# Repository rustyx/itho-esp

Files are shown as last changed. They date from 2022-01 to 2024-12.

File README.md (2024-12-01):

## itho-esp

Itho diag port controller

### WTF is this?

This is an ESP32 firmware that connects to the dianostic port of an Itho device in order to communicate with it and let it do things it couldn't before.

Originally designed for controlling the Itho HRU ecofan 350 ventilation unit via MQTT, but can be used to play with the I2C bus of many other Itho products.

Some key features are:

* I2C bus sniffing - dumps messages to/from the Itho CPU. On products that have peripherals like an RFT receiver, will dump traffic between the peripheral and the CPU.
* Send and receive dianostic messages to the CPU.
* Query the device status and parse parameter values.
* Control the device via Wi-Fi/MQTT.
* Monitor temperature and humidity via DHT22 and/or SHT4x, publish results via MQTT.
* (HRU-specific) Control ventilation level setting (low, med., high) via MQTT.
* (HRU-specific) Automatically set ventilation to high when humidity exceeds a threshold value.

### Prerequisites

Hardware:

* An Itho ecofan HRU 350 WTW unit (or another Itho product that has an RJ45 diagnostic port)
* ESP32 Dev Kit (or a raw ESP32 unit + power supply + a USB COM dongle + some SMD work)
* a logic level shifter for converting 5V <-> 3,3V logic levels (or 2 small N-channel MOSFETs)
* One or more DHT22 or SHT4x (optional, to measure humidity)
* DC-DC buck converter (optional, to power ESP32 directly from the Itho diag port's +15V)

Software:

* [ESP-IDF Framework](https://docs.espressif.com/projects/esp-idf/en/latest/esp32/get-started/index.html) v5.3+ and its prerequisites (`xtensa-esp32-elf-gcc`, `pip`, etc.)
* USB COM driver matching the USB serial interface chip (see [Connect ESP32 to PC](https://docs.espressif.com/projects/esp-idf/en/latest/esp32/get-started/establish-serial-connection.html))
* [Visual Studio Code](https://code.visualstudio.com/download) with [ESP-IDF extension](https://github.com/espressif/vscode-esp-idf-extension/blob/master/docs/ONBOARDING.md) (optional but recommended, will also help with installing the ESP-IDF framework)

### Building

* Make sure the ESP Dev Kit can be connected to USB and a COM port is functional
* Install ESP-IDF framework, make sure it works and has access to the COM port (see [connect your device](https://docs.espressif.com/projects/esp-idf/en/latest/esp32/get-started/#get-started-connect))
* Build the firmware: `idf.py build`
* Flash the firmware: `idf.py -b 921600 flash` (will also invoke `build` if needed)  
  To flash, the ESP32 chip needs to be put in download mode. This can be achieved by shorting J3 pin 5 to ground (pin 4) while booting.
* Attach to the console: `idf.py monitor` (can combine with the `flash` command)

### Console interface

* `config` : Configure Wi-Fi, MQTT and humidity sensor GPIO
* `p` : Pullup OFF
* `P` : Pullup ON
* `s` : Sniffer OFF
* `S` : Sniffer ON
* `h` : Hex reporting OFF
* `H` : Hex reporting ON
* Or any of MQTT command below

### MQTT commands

* `set1` - set ventilation level to low
* `set2` - set ventilation level to medium
* `set3` - set ventilation level to high for 30 min (then back to low)
* `hum` - request DHT22 temp/humidity values
* `status` - request device status
* `ping` - request `pong`
* `high_hum_threshold` - get current high humidity threshold (output goes to `esp-data-dht`)
* `high_hum_threshold N` - set high humidity threshold to N * 0.1% (e.g. for 75% use 750)
* Hex bytes - send these bytes to the bus

### MQTT topics

`esp` - The topic for MQTT requests.

`esp-data` - The topic for MQTT replies. In addition, Itho status data + DHT data are published here as a JSON array every 5 seconds.

`esp-data-dht` - DHT data (humidity, temp, status) is published here when `hum` is requested.

`esp-data-hex` - when hex reporting is enabled, all Itho response messages are published here in hex format.

### Tech specs

For technical details and other research notes refer to [Specs.md](Specs.md)

### License

The unlicense:

The software is provided AS-IS without any warranty.

You can do whatever you want with it to the extent permitted by law.

I will deny any involvement with this project, should any questions arise.

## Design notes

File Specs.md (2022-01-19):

### RJ45 dianostic port pinout

| Pin | |
| --- | ---- |
| 2 | SCL  |
| 3 | GND  |
| 4 | GND  |
| 5 | +15V |
| 7 | SDA  |

The SCL, SDA are I2C lines with a 5V pull-up (5,6K) connecting straight to the CPU on the Itho mainboard.

+15V can be used for power supply needs (appears to be good for at least 1A).

There is no +5V available, but is not needed due to the built-in pull-ups (the lines only need to be pulled down for a logical 0).

---

### GPIO Pin assignment

| GPIO | Desc | Notes |
| ---- | --- | --- |
| 0 | Reset | The ESP32 reset pin (inverted) |
| 13 | I2C Sniffer SDA | Defined in [i2c_sniffer.h](main/i2c_sniffer.h) |
| 14 | I2C Slave SDA | Defined in [i2c_slave.h](main/i2c_slave.h) |
| 15 | DHT22 I/O | Defined in [dht.h](main/dht.h) |
| 25 | I2C Sniffer SCL | |
| 26 | I2C Master SCL  | Defined in [i2c_master.h](main/i2c_master.h) |
| 27 | I2C Master SDA  | |
| 33 | I2C Slave SCL | |

The I2C pins were carefully chosen so that they can be wired into a "bus", as can be seen on the schematic:

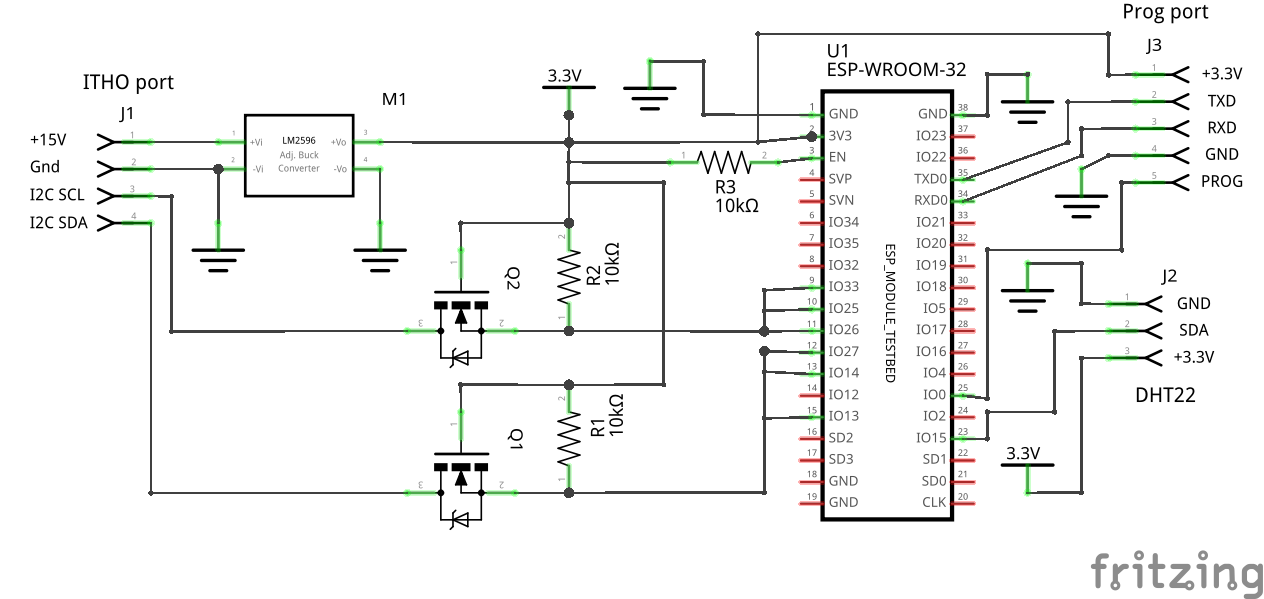
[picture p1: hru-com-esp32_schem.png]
schematic


---

### I2C message format

The Itho mainboard is an I2C master running at ~100kHz.  
Each packet has a checksum byte at the end, which is the negative sum of all other bytes.  
First byte is destination address (0x82 = Itho mainboard).  
Second byte is reply address (0x80 = dongle).  
2 bytes: message code.  
1 byte: message flags (it seems:  `06` = write, `04` = request, `01` = reply).  
1 byte: payload length (N).  
N bytes: payload.  
1 byte: checksum.  

---

### Message `90 E0`: query device type

82 80 90 E0 04 00 8A

Example reply:

80 82 90 E0 01 12 00 01 00 03 12 0B 00 00 00 FF FF FF FF FF FF FF FF 00 62

`00` = Manufacturer (Itho), `03` = Device type (HRU), `12` = HW version, `0B` = list version.

The "list version" refers to the Datalabel_V.. table in the corresponding Jet DB (.par) file of the Servicetool.

Some known Device Type codes:

`01` : Lucht gordijn  
`03` : HRU ECO-fan  
`08` : Laadboiler  
`0A` : Gas gestookte boost boiler  
`0B` : DemandFlow  
`0C` : CO2 relay  
`0D` : Warmtepomp  
`0E` : Oplaadboiler enkele wisselaar  
`0F` : AutoTemp  
`10` : Oplaadboiler dubbele wisselaar  
`11` : RF+  
`14` : CVE  
`15` : Extended  
`16` : Extended Plus  
`1A` : AreaFlow  
`1B` : CVE-Silent  
`1C` : CVE-SilentExt  
`1D` : CVE-SilentExtPlus  
`20` : RF_CO2  
`2B` : HRU 350

---

### Message `90 E1`: query device serial number

82 80 90 E1 04 00 89

Example reply (edited):

80 82 90 E1 01 03 52 D3 3C 48

Serial nr: 52D33C = 5428028

---

### Message `A4 00`: query status format

82 80 A4 00 04 00 56

Example reply:

80 82 A4 00 01 16 91 11 10 90 10 90 92 92 00 92 92 00 00 91 00 10 10 00 90 00 00 10 C8

A4 00 01 followed by number of data elements, followed by element formats (1 byte per element).

Data format (1 byte):

| Bit  | Description |
| ---- | --- |
| 7 | signed (1) / unsigned (0) |
| 6..4 | size in bytes (2^n): 0=1, 1=2, 2=4 |
| 3..0 | decimal digits (divider 10^n) |

So for example `91` would mean "signed, 2 bytes, 0.1 values".

Special cases:

0C: unsigned 1 byte  
0F: unsigned 1 byte * 0.5  
5B: unsigned 2 bytes  
6C: 1 byte boolean

---

### Message `A4 01`: query device status

82 80 A4 01 04 00 55

Example reply:

80 82 A4 01 01 25 00 00 03 9C 03 9E 03 98 03 EB 03 EB 09 09 09 8A 00 09 09 09 8A 00 00 0B B8 01 00 00 00 B1 79 00 00 00 00 10 95 9F

80 82 A4 01 01 followed by data size and data formatted according to the status format (see previous message).

The temperatures are the bytes 09 09 09 8A, or (0x0909 and 0x098A) 23.13 C en 24.42 C respectively (.01 values).

The first 00 00 is the ventilation level. It goes from 0 for position "1" to 03E8 (100.0) for level "3".

For the meaning of each data element refer to [Itho Data Labels.xlsx](Itho%20Data%20Labels.xlsx)

---

### Itho ecofan RFT 536-0124 (RF remote control) messages

Button 1:  
82 60 C1 01 01 11 (4b: msg timestamp) (1b: msg format) (3b: commander ID) (1b: command seq nr) 22 F1 03 00 02 04 (2b: seq) (1b: checksum)

Button 2:  
82 60 C1 01 01 11 (4b: msg timestamp) (1b: msg format) (3b: commander ID) (1b: command seq nr) 22 F1 03 00 03 04 (2b: seq) (1b: checksum)

Button 3:  
82 60 C1 01 01 11 (4b: msg timestamp) (1b: msg format) (3b: commander ID) (1b: command seq nr) 22 F1 03 00 04 04 (2b: seq) (1b: checksum)

Button 4 (1st press):  
82 60 C1 01 01 11 (4b: msg timestamp) (1b: msg format) (3b: commander ID) (1b: command seq nr) 22 F3 03 00 00 0A (2b: seq) (1b: checksum)

Button 4 (2nd press):  
82 60 C1 01 01 11 (4b: msg timestamp) (1b: msg format) (3b: commander ID) (1b: command seq nr) 22 F3 03 00 00 14 (2b: seq) (1b: checksum)

Button 4 (3rd press):  
82 60 C1 01 01 11 (4b: msg timestamp) (1b: msg format) (3b: commander ID) (1b: command seq nr) 22 F3 03 00 00 1E (2b: seq) (1b: checksum)

Register an RFT (press 1+4 or 2+3):  
82 60 C1 01 01 1A (4b: msg timestamp) (1b: msg format) (3b: commander ID) (1b: command seq nr) 1F C9 0C 00 22 F1 (3b: commander ID) 01 10 E0 (3b: commander
ID) (2b: seq) (1b: checksum)

Deregister an RFT (press 1+2+3+4):  
82 60 C1 01 01 14 (4b: msg timestamp) (1b: msg format) (3b: commander ID) (1b: command seq nr) 1F C9 06 00 1F C9 (3b: commander ID) (2b: seq) (1b: checksum)

Notes:

* Each command is repeated 3 times with a short interval
* Note sure if my interpretation of (4b: msg timestamp), (1b: command seq nr), (2b: seq) is correct, most can be `00`'s but some itho devices (but not the HRU) need to have the command seq nr changed every message.
* (3b: commander ID) are the 3 bytes of the device ID
* (1b: msg format) is the message format determining the fields present in the message. For standard 4 button remotes this is `16`.

...

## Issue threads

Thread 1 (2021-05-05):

Datamessage explained a little further

Ierlandfan, 2021-05-05:
Can you explain the data messages a little further? Trying to understand their meanings.

Data format return of an Itho Eco Fan CVS silent: (1B)

80 82 A4 00 01
0C
80 10 10 10 00 10 20 10 10 00 92 92 29
12 datatypes. (0C)  with their formats.
29 is checksum. So far so good.

But then it gets a little blurry.
Status query return:

80 82 A4 01 01

17 64 01 C2 01 C6 00 10 04 02 01 00 00 28 22 00 00 82 00 EF 82 00 82 00 7D

Am I correct that there are 12 size definitions and 12 payloads according to data format and observations?
7d is checksum.

17 64....
64 is payload.
Translates to 100 in decimals.
That would read 10. Is that correct?
10000000 is format, signed, 1 byte, 10^0.

How do the data labels correlate with these?

rustyx, 2021-05-06:
80: signed, 1 byte, 0 decimals
10: unsigned, 2 bytes, 0 decimals
00: unsigned, 1 byte, 0 decimals
20: unsigned, 4 bytes, 0 decimals
92: signed, 2 bytes, 2 decimals (value * 0.01)

So "80 10 10 10 00 10 20 10 10 00 92 92" would be 12 values, for a total of 23 bytes.

Then we group the data bytes according to this definition:

"64 01C2 01C6 0010 04 0201 00002822 0000 8200 EF 8200 8200"

In decimal it becomes

100, 450, 454, 4, 513, 10274, 0, 33280, 239, -322.56, -322.56

Not sure about the formatting of the last two values, it looks strange. What's the full device type response (80 82 90 E0 01...)?

Ierlandfan, 2021-05-06:
Device type:
80 82 90 E0 01 25 00 01 00 1B 37 1B 01 FE FF FF FF FF FF 1D 08 07 E3 43 56 45 2D 52 46 00 00 00 00 00 00 00 00 00 00 00 00 00 00 4E

rustyx, 2021-05-07:
Yes it's a CVE-Silent rev 55, datalabels v.27. Added it to the [Itho Data Labels.xlsx](https://github.com/rustyx/itho-esp/blob/main/Itho%20Data%20Labels.xlsx)

There are 12 data labels which correspond to the values

100, 450, 454, 16, 4, 513, 10274, 0, 33280, 239, -322.56, -322.56

The formatting seems to be correct, so not sure why the weird temp values... do they ever change? If not, then maybe it doesn't have a temp sensor.

Ierlandfan, 2021-05-07:
Now I also understand the datalabels:

Device Type:
80
82 Manufacturergroup
90 Manufacturer
E0
01
25
00
01
00
1B Device (13) CVS_Silent
37 Productversion (55)
1B Listversion (27)

Device (13) correlates (somehow) to the (weak password protected) $_parameters_SilentBasic.par database in the  Itho Service tool. Listversion 27 correlates to Datalabel_V27 in that database.

The temp sensor is indeed not present.

rustyx, 2021-06-15:
Correct, except Device CVS_Silent is 27 (0x1B). Those mappings are hardcoded in the servicetool.

Closed 2021-06-15.

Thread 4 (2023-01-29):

Build fails on undeclared constant ESP_MAC_WIFI_STA

philipkocanda, 2023-01-29:
```
$ idf.py build
```

```
../main/Config.cpp: In member function 'bool Config::Read()':
../main/Config.cpp:39:32: error: 'ESP_MAC_WIFI_STA' was not declared in this scope; did you mean 'ESP_IF_WIFI_STA'?
   39 |     int rc = esp_read_mac(mac, ESP_MAC_WIFI_STA);
      |                                ^~~~~~~~~~~~~~~~
      |                                ESP_IF_WIFI_STA
../main/Config.cpp:39:14: error: 'esp_read_mac' was not declared in this scope
   39 |     int rc = esp_read_mac(mac, ESP_MAC_WIFI_STA);
      |              ^~~~~~~~~~~~
../main/Config.cpp:47:17: error: 'struct mqtt_config_t' has no member named 'client_id'
   47 |     mqtt_config.client_id = mqttId.c_str();
      |                 ^~~~~~~~~
../main/Config.cpp:48:17: error: 'struct mqtt_config_t' has no member named 'uri'
   48 |     mqtt_config.uri = mqtturi.c_str();
      |                 ^~~
../main/Config.cpp:49:17: error: 'struct mqtt_config_t' has no member named 'cert_pem'
   49 |     mqtt_config.cert_pem = trimToNull(mqttServerCert.c_str());
      |                 ^~~~~~~~
../main/Config.cpp:50:17: error: 'struct mqtt_config_t' has no member named 'client_key_pem'
   50 |     mqtt_config.client_key_pem = trimToNull(mqttClientKey.c_str());
      |                 ^~~~~~~~~~~~~~
../main/Config.cpp:51:17: error: 'struct mqtt_config_t' has no member named 'client_cert_pem'
   51 |     mqtt_config.client_cert_pem = trimToNull(mqttClientCert.c_str());
      |                 ^~~~~~~~~~~~~~~
```

Environment:
- Ubuntu 20.04 (amd64)
- ESP-IDF v5.1-dev-3066-g236fa5e669

philipkocanda, 2023-01-29:
Never mind, downgraded to ESP-IDF v4.4 and it compiled without issues. In case anyone is looking for it, here's how to do it (will remove existing esp-idf version):

```sh
cd ~/esp
rm -rf esp-idf
git clone -b v4.4.3 --recursive https://github.com/espressif/esp-idf.git

cd ~/esp/esp-idf
./install.sh esp32
```

Closed 2023-01-29.

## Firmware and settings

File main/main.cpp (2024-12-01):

#include "Config.h"
#include "Nvs.h"
#include "console.h"
#include "dht.h"
#include "sht4x.h"
#include "i2c_master.h"
#include "i2c_slave.h"
#include "i2c_sniffer.h"
#include "mqtt.h"
#include "util.h"
#include "wifi.h"
#include <algorithm>
#include <driver/uart.h>
#include <esp_event.h>
#include <esp_log.h>
#include <esp_system.h>
#include <freertos/FreeRTOS.h>
#include <freertos/event_groups.h>
#include <freertos/queue.h>
#include <freertos/task.h>
#include <string.h>

static const char* TAG = "main";

static char cmd[128];
static uint8_t buf[128];
static uint32_t cmdlen = 0;
static struct {
    int ret = -1, hum = -1, temp = -1;
} dht_ret[max_sensors];
static bool verbose = false, reportHex = false;

Nvs nvs;
Config config;

bool sendBytes(const uint8_t* buf, size_t len) {
    if (len) {
        esp_err_t rc = i2c_master_send((char*)buf, len);
        if (rc || verbose) {
            printf("Master send: %d\n", rc);
        }
        return rc == ESP_OK;
    }
    return false;
}

bool sendBytesHex(const char* hex, size_t hexlen) {
    size_t len = parseHexStr(hex, hexlen, buf, sizeof(buf));
    return sendBytes(buf, len);
}

static void publishHumidity() {
    char buf[20 * max_sensors];
    int len = 0;
    for (int i = 0; i < max_sensors; i++) {
        auto& ret = dht_ret[i];
        len += snprintf(buf + len, sizeof(buf) - len, "%c%d.%d,%d.%d,%d", len ? ',' : '[', ret.hum / 10, ret.hum % 10, ret.temp / 10, ret.temp % 10,
                 ret.ret);
    }
    strncpy(buf + len, "]", sizeof(buf) - 1);
    mqtt_publish("esp-data-dht", buf);
}

static uint8_t set1[]{0x82, 0x60, 0xC1, 0x01, 0x01, 0x11, 0x00, 0x00, 0x00, 0x00, 0xFF, 0xFF,
                      0xFF, 0xFF, 0x00, 0x22, 0xF1, 0x03, 0x00, 0x02, 0x04, 0x00, 0x00, 0xCC};
static uint8_t set2[]{0x82, 0x60, 0xC1, 0x01, 0x01, 0x11, 0x00, 0x00, 0x00, 0x00, 0xFF, 0xFF,
                      0xFF, 0xFF, 0x00, 0x22, 0xF1, 0x03, 0x00, 0x03, 0x04, 0x00, 0x00, 0xCC};
static uint8_t set3[]{0x82, 0x60, 0xC1, 0x01, 0x01, 0x11, 0x00, 0x00, 0x00, 0x00, 0xFF, 0xFF,
                      0xFF, 0xFF, 0x00, 0x22, 0xF3, 0x03, 0x00, 0x00, 0x1E, 0x00, 0x00, 0xCC};

static void initRFTKey(uint32_t rftKey) {
    memcpy(set1 + 10, &rftKey, 4);
    fixChecksum(set1, sizeof(set1));
    memcpy(set2 + 10, &rftKey, 4);
    fixChecksum(set2, sizeof(set2));
    memcpy(set3 + 10, &rftKey, 4);
    fixChecksum(set3, sizeof(set3));
}

static int64_t lastSetTime;

static void processCommand(const char* data, int data_len) {
    if (strncmp("set1", data, data_len) == 0) {
        lastSetTime = std::max(lastSetTime, esp_timer_get_time()) + 3600 * 1000000LL;
        sendBytes(set1, sizeof(set1));
    } else if (strncmp("set2", data, data_len) == 0) {
        sendBytes(set2, sizeof(set2));
    } else if (strncmp("set3", data, data_len) == 0) { // 30min
        sendBytes(set3, sizeof(set3));
    }
    // } else if (strncmp("sniff0", data, data_len) == 0) {
    //     i2c_sniffer_disable();
    //     reportHex = false;
    //     mqtt_publish("esp-data", "sniffer off");
    // } else if (strncmp("sniff1", data, data_len) == 0) {
    //     i2c_sniffer_enable();
    //     reportHex = true;
    //     mqtt_publish("esp-data", "sniffer on");
    // } else if (strncmp("rftkey", data, 6) == 0) {
    //     unsigned i = 6;
    //     while (data[i] == ' ')
    //         i++;
    //     if (i < data_len) {
    //         uint32_t key = 0;
    //         parseHexStr(data + i, data_len - i, (uint8_t*)&key, 4);
    //         if (key) {
    //             config.rftKey = key;
    //             initRFTKey(config.rftKey);
    //             if (!config.Write()) {
    //                 ESP_LOGE(TAG, "Config write failed");
    //             }
    //         }
    //     }
    //     std::string s = "rftkey=";
    //     s += toHexStr((uint8_t*)&config.rftKey, 4);
    //     mqtt_publish("esp-data", s.c_str());
    else if (strncmp("high_hum_threshold", data, 18) == 0) {
        unsigned i = 18;
        while (data[i] == ' ')
            i++;
        if (i < data_len) {
            std::string hum_str(data + i, data + data_len);
            int hum = atoi(hum_str.c_str());
            if (hum < 100 || hum > 1000) {
                std::string buf = "invalid parameter value " + hum_str;
                ESP_LOGE(TAG, "%s", buf.c_str());
                mqtt_publish("esp-data-dht", buf.c_str());
                return;
            }
            config.high_hum_threshold = Config::normalize_high_hum_threshold(hum);
            if (!config.Write()) {
                ESP_LOGE(TAG, "Config write failed");
            }
        }
        int hum1 = config.high_hum_threshold / 10, hum2 = config.high_hum_threshold % 10;
        std::string buf = "high_hum_threshold=" + std::to_string(hum1) + '.' + std::to_string(hum2);
        ESP_LOGI(TAG, "%s", buf.c_str());
        mqtt_publish("esp-data-dht", buf.c_str());
    } else if (strncmp("hum", data, data_len) == 0) {
        publishHumidity();
    } else if (isHex(data[0])) {
        sendBytesHex(data, data_len);
    } else {
        ESP_LOGE(TAG, "Unknown command '%s'", std::string(data, data + data_len).c_str());
    }
}

static const int mode_set_max_freq_sec = 600; // set mode at most once every 10 min
static int prev_hum;

static void handleHumidity() {
    int hum = 0;
    for (int i = 0; i < max_sensors; i++ ) {
        hum = std::max(hum, dht_ret[i].hum);
    }
    if (hum >= config.high_hum_threshold && prev_hum >= config.high_hum_threshold) {
        int64_t now = esp_timer_get_time();
        if (now - lastSetTime >= mode_set_max_freq_sec * 1000000) {
            ESP_LOGI(TAG, "High humidity, setting mode 3");
            processCommand("set3", 4);
        }
    }
    prev_hum = hum;
}

static void processConsoleCommand() {
    if (strcmp(cmd, "p") == 0) {
        i2c_sniffer_pullup(false);
        printf("Pullup OFF\n");
    } else if (strcmp(cmd, "P") == 0) {
        i2c_sniffer_pullup(true);
        printf("Pullup ON\n");
    } else if (strcmp(cmd, "s") == 0) {
        i2c_sniffer_disable();
        printf("Sniffer OFF\n");
    } else if (strcmp(cmd, "S") == 0) {
        i2c_sniffer_enable();
        printf("Sniffer ON\n");
    } else if (strcmp(cmd, "h") == 0) {
        reportHex = false;
        printf("esp-data-hex reporting OFF\n");
    } else if (strcmp(cmd, "H") == 0) {
        reportHex = true;
        printf("esp-data-hex reporting ON\n");
    } else if (strcmp(cmd, "r") == 0) {
        printf("Restarting\n");
        vTaskDelay(configTICK_RATE_HZ / 4);
        esp_restart();
    } else if (strcmp("config", cmd) == 0) {
        if (config.Reconfigure()) {
            i2c_sniffer_enable();
            printf("Sniffer is ON.\n"
                   "Press any key on the RFT device, watching for a message that looks like:\n"
                   "82 60 C1 01 01 11 .. .. .. .. xx xx xx xx .. .. .. .. .. .. .. .. .. ..\n"
                   "The RFT ID will be the values xx xx xx xx.\n"
                   "Write those down, then turn off the sniffer with the 's' command.\n");
        }
    } else {
        processCommand(cmd, strlen(cmd));
    }
}

portMUX_TYPE status_mux = portMUX_INITIALIZER_UNLOCKED;
std::string datatypes;

static void requestStatus() {
    for (int i = 0; i < 3; ++i) {
        portENTER_CRITICAL(&status_mux);
        bool haveDatatypes = !datatypes.empty();
        portEXIT_CRITICAL(&status_mux);
        if (haveDatatypes)
            break;
        sendBytesHex("82 80 A4 00 04 00 56", 20);
        vTaskDelay(configTICK_RATE_HZ / 5);
    }
    if (datatypes.empty()) {
        ESP_LOGW(TAG, "Unable to fetch data types");
    }
    sendBytesHex("82 80 A4 01 04 00 55", 20);
}

static void requestStatusTask(void* arg) {
    requestStatus();
    vTaskDelete(nullptr);
}

static void requestStatusLoopTask(void* arg) {
    for (;;) {
        vTaskDelay(5 * configTICK_RATE_HZ);
        if (mqtt_is_connected()) {
            requestStatus();
        }
    }
    vTaskDelete(nullptr);
}

/*
    Data format (1 byte):
    bit 7: signed / unsigned
    bits 6..4: size (2^n): 0=1, 1=2, 2=4
    bits 3..0: decimal digits (divider 10^n)
*/
void handleStatus(const uint8_t* data, size_t len) {
    std::string s;
    char buf[64];
    s.reserve(4 * len + 4);
    s = "[";
    size_t i = 0;
    for (uint8_t dt : datatypes) {
        if (i >= len)
            break;
        if (s.length() > 1)
            s += ',';
        int32_t x = (dt & 0x80) ? (int8_t)data[i++] : data[i++];
        for (int j = (1 << ((dt >> 4) & 3)); j > 1; --j) {
            x = (x << 8) | data[i++];
        }
        int rem = dt & 7;
        snprintf(buf, sizeof(buf), "%0*ld", (int)(rem + 1 + (x < 0)), (long int)x);
        size_t len = strlen(buf);
        s.append(buf, len - rem);
        if (rem) {
            s += '.';
            s.append(buf + len - rem, rem);
        }
    }
    for (int i = 0; i < max_sensors; i++) {
        if (!config.sensors[i].type) {
            continue;
        }
        auto& ret = dht_ret[i];
        snprintf(buf, sizeof(buf), ",%d.%d,%d.%d,%d", ret.hum / 10, ret.hum % 10, ret.temp / 10, ret.temp % 10, ret.ret);
        s += buf;
    }
    s += "]";
    mqtt_publish_bin("esp-data", s.c_str(), s.length());
}

inline bool checksumOk(const uint8_t* data, size_t len) { return checksum(data, len - 1) == data[len - 1]; }

void i2c_slave_callback(const uint8_t* data, size_t len) {
    std::string s = toHexStr(data, len);
    if (len > 6 && data[1] == 0x82 && data[2] == 0xA4 && data[3] == 0 && data[4] == 1 && data[5] < len - 5 && checksumOk(data, len)) {
        portENTER_CRITICAL(&status_mux);
        datatypes.assign((const char*)data + 6, data[5]);
        portEXIT_CRITICAL(&status_mux);
    }
    if (len > 6 && data[1] == 0x82 && data[2] == 0xa4 && data[3] == 1 && data[4] == 1 && data[5] < len - 5 && checksumOk(data, len)) {
        handleStatus(data + 6, len - 7);
    }
    if (reportHex) {
        mqtt_publish_bin("esp-data-hex", s.c_str(), s.length());
    }
    if (verbose) {
        printf("Slave: %s\n", s.c_str());
    }
}

static void processMqttCommand(const char* data, int data_len) {
    if (strncmp("status", data, data_len) == 0) {
        xTaskCreate(requestStatusTask, "requestStatusTask", 4096, NULL, 6, NULL);
    } else if (strncmp("ping", data, data_len) == 0) {
        mqtt_publish("esp-data", "pong");
    } else {
        processCommand(data, data_len);
    }
}

static void mqtt_message_callback(const char* topic, int topic_len, const char* data, int data_len) {
    processMqttCommand(data, data_len);
    // ESP_LOGD(TAG, "mqtt_callback '%.*s' '%.*s'", topic_len, topic, data_len, data);
}

static void mqtt_connect_callback() { mqtt_subscribe("esp", mqtt_message_callback); }

static void dht_task(void* arg) {
    int id = (int)arg;
    DHT dht(("DHT" + std::to_string(id + 1)).c_str(), (gpio_num_t)config.sensors[id].sda);
    int errors = 1;
    auto& ret = dht_ret[id];
    while (1) {
        vTaskDelay(5 * configTICK_RATE_HZ); // wait at least 2 sec before reading again
        ret.ret = dht.readDHT();
        if (!dht.errorHandler(ret.ret)) {
            if (errors && ++errors > 3) {
                ESP_LOGI(TAG, "Stopping DHT[%d] task", id + 1);
                break;
            }
            continue;
        }
        errors = 0;
        ret.hum = dht.getHumidity();
        ret.temp = dht.getTemperature();
        ESP_LOGI(TAG, "DHT[%d] Humidity %d.%d, Temp %d.%d", id + 1, ret.hum / 10, ret.hum % 10, ret.temp / 10, ret.temp % 10);
        handleHumidity();
    }
    vTaskDelete(nullptr);
}

static void sht4x_task(void* arg) {
    int id = (int)arg;
    SHT4x sht(("SHT" + std::to_string(id + 1)).c_str(), (gpio_num_t)config.sensors[id].sda, (gpio_num_t)config.sensors[id].scl);
    int errors = 1;
    i2c_err_t res = sht.readSerial();
    sht.errorHandler(res);
    ESP_LOGI(TAG, "SHT4x[%d] serial: %" PRIu32, id + 1, sht.getSerial());
    auto& ret = dht_ret[id];
    while (1) {
        vTaskDelay(5 * configTICK_RATE_HZ);
        i2c_err_t res = sht.measure();
        ret.ret = (int)res;
        if (!sht.errorHandler(res)) {
            if (errors && ++errors > 3) {
                ESP_LOGI(TAG, "Stopping SHT4x[%d] task", id + 1);
                break;
            }
            continue;
        }
        errors = 0;
        ret.hum = sht.getHumidity();
        ret.temp = sht.getTemperature();
        ESP_LOGI(TAG, "SHT4x[%d] Humidity %d.%d, Temp %d.%d", id + 1, ret.hum / 10, ret.hum % 10, ret.temp / 10, ret.temp % 10);
        handleHumidity();
    }
    vTaskDelete(nullptr);
}

extern "C" void app_main() {
    setvbuf(stdout, NULL, _IONBF, 0);
    uart_driver_install(UART_NUM_0, 512, 512, 32, NULL, ESP_INTR_FLAG_LEVEL1);
    // esp_log_level_set("*", ESP_LOG_INFO);
    // esp_log_level_set("SHT4x", ESP_LOG_DEBUG);
    nvs.Init();
    config.Read();
    initRFTKey(config.rftKey);
    i2c_sniffer_init(false);
    i2c_master_init();
    i2c_slave_init(&i2c_slave_callback);
    wifi_init();
    mqtt_init();
    mqtt_on_connect(&mqtt_connect_callback);
    for (int i = 0; i < config.sensors.size(); i++) {
        switch (config.sensors[i].type) {
            case SensorTypeDHT:
                xTaskCreatePinnedToCore(&dht_task, ("dht_task" + std::to_string(i)).c_str(), 4096, (void*)i, 7, NULL, 0);
                break;
            case SensorTypeSHT4x:
                xTaskCreatePinnedToCore(&sht4x_task, ("sht4x_task" + std::to_string(i)).c_str(), 4096, (void*)i, 7, NULL, 0);
                break;
        }
    }
    xTaskCreatePinnedToCore(requestStatusLoopTask, "statusLoopTask", 4096, NULL, 8, NULL, 1);

    printf("Press Enter to start console\n");
    while (1) {
        int len = uart_read_bytes(UART_NUM_0, (uint8_t*)buf, 1, configTICK_RATE_HZ / 5);
        if (len > 0 && *buf == '\r') {
            break;
        }
    }
    printf("\nConsole started\n");
    verbose = true;
    while (1) {
        int len = uart_read_bytes(UART_NUM_0, (uint8_t*)buf, sizeof(buf), 2);
        if (len > 0) {
            for (int i = 0; i < len; ++i) {
                if (buf[i] == '\r')
                    buf[i] = '\n';
            }
            // uart_write_bytes(UART_NUM_0, buf, len);
            printf("%.*s", len, buf);
            if (buf[0] == '\n')
                printf("\n");
            for (int i = 0; i < len; ++i) {
                if (buf[i] == '\n' || buf[i] == '\r') {
                    // if (buf[i] == '\n')
                    //     printf("\n");
                    cmd[cmdlen] = 0;
                    if (cmdlen)
                        processConsoleCommand();
                    cmdlen = 0;
                } else {
                    cmd[cmdlen++] = buf[i];
                    if (cmdlen == sizeof(cmd)) {
                        printf("Command too long\n");
                        cmdlen = 0;
                        break;
                    }
                }
            }
        }
    }
}

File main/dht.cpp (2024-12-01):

/*------------------------------------------------------------------------------
    DHT22 CPP temperature & humidity sensor AM2302 (DHT22) driver for ESP32
    Jun 2017: Ricardo Timmermann, new for DHT22
        Timing model entirely rewritten by rustyx

    This example code is in the Public Domain (or CC0 licensed, at your option.)
    Unless required by applicable law or agreed to in writing, this
    software is distributed on an "AS IS" BASIS, WITHOUT WARRANTIES OR
    CONDITIONS OF ANY KIND, either express or implied.
    PLEASE KEEP THIS CODE IN LESS THAN 0XFF LINES. EACH LINE MAY CONTAIN ONE BUG !!!
---------------------------------------------------------------------------------*/

#include "dht.h"
#include <esp_err.h>
#include <esp_log.h>
#include <freertos/FreeRTOS.h>
#include <stdint.h>
#include <string.h>
#include <sys/types.h>

DHT::DHT(const char* tg, gpio_num_t pin) : dhtGpio(pin) {
    strncpy(tag, tg, sizeof(tag));
    ESP_LOGI(tag, "Starting DHT on GPIO %d", dhtGpio);
    gpio_config_t config{BIT64(dhtGpio), GPIO_MODE_INPUT, GPIO_PULLUP_DISABLE, GPIO_PULLDOWN_DISABLE, GPIO_INTR_DISABLE};
    gpio_config(&config);
}

bool DHT::errorHandler(int response) {
    switch (response) {
    case DHT_TIMEOUT_ERROR:
        ESP_LOGE(tag, "Sensor timeout");
        break;
    case DHT_CHECKSUM_ERROR:
        ESP_LOGE(tag, "Checksum error");
        break;
    case DHT_OK:
        break;
    default:
        ESP_LOGE(tag, "Unknown error");
    }
    return response == DHT_OK;
}

inline int DHT::waitForLevel(int usTimeOut, bool state) {
    int uSec = 0;
    while (gpio_get_level(dhtGpio) != state) {
        if (uSec > usTimeOut) {
            uSec = -1;
            break;
        }
        ++uSec;
        esp_rom_delay_us(1); // uSec delay
    }
    return uSec;
}

/*----------------------------------------------------------------------------
;
;    read DHT22 sensor

    copy/paste from AM2302/DHT22 Docu:
    DATA: Hum = 16 bits, Temp = 16 Bits, check-sum = 8 Bits
    Example: MCU has received 40 bits data from AM2302 as
    0000 0010 1000 1100 0000 0001 0101 1111 1110 1110
    16 bits RH data + 16 bits T data + check sum

    1) we convert 16 bits RH data from binary system to decimal system, 0000 0010 1000 1100 → 652
    Binary system Decimal system: RH=652/10=65.2%RH
    2) we convert 16 bits T data from binary system to decimal system, 0000 0001 0101 1111 → 351
    Binary system Decimal system: T=351/10=35.1°C
    When highest bit of temperature is 1, it means the temperature is below 0 degree Celsius.
    Example: 1000 0000 0110 0101, T= minus 10.1°C: 16 bits T data
    3) Check Sum=0000 0010+1000 1100+0000 0001+0101 1111=1110 1110 Check-sum=the last 8 bits of Sum=11101110

    Signal & Timings:
    The interval of whole process must be beyond 2 seconds.

    To request data from DHT:
    1) Sent low pulse for > 1~10 ms (MILI SEC)
    2) Sent high pulse for > 20~40 us (Micros).
    3) When DHT detects the start signal, it will pull low the bus 80us as response signal,
       then the DHT pulls up 80us for preparation to send data.
    4) When DHT is sending data to MCU, every bit's transmission begin with low-voltage-level that last 50us,
       the following high-voltage-level signal's length decide the bit is "1" or "0".
        0: 26~28 us
        1: 70 us
;----------------------------------------------------------------------------*/

#define MAXdhtData 5 // to complete 40 = 5*8 Bits

int DHT::readDHT() {
    int uSec = 0;
    uint8_t dhtData[MAXdhtData] = {};
    uint8_t byteInx = 0;
    uint8_t bitInx = 7;

    // == Send start signal to DHT sensor ===========

    gpio_set_direction(dhtGpio, GPIO_MODE_OUTPUT);

    // pull down for 5 ms for a smooth and nice wake up
    gpio_set_level(dhtGpio, 0);
    esp_rom_delay_us(5000);

    portENTER_CRITICAL(&mutex);
    // pull up for 25 us to gently ask for data
    gpio_set_level(dhtGpio, 1);
    esp_rom_delay_us(25);

    gpio_set_direction(dhtGpio, GPIO_MODE_INPUT);

    // == DHT will keep the line low for 80 us and then high for 80us ====

    int uSec1 = waitForLevel(50, 0);
    if (uSec1 < 0) {
        portEXIT_CRITICAL(&mutex);
        return DHT_TIMEOUT_ERROR;
    }

    // -- 80us up ------------------------

    int uSec2 = waitForLevel(100, 1);
    // ESP_LOGD(tag, "Response 2 = %d", uSec2);
    if (uSec2 < 0) {
        portEXIT_CRITICAL(&mutex);
        // ESP_LOGW(tag, "Sensor timeout 2");
        return DHT_TIMEOUT_ERROR;
    }

    // == No errors, read the 40 data bits ================

    for (int k = 0; k < 40; k++) {
        // -- starts new data transmission with low signal
        uSec = waitForLevel(100, 0);
        if (uSec < 0) {
            portEXIT_CRITICAL(&mutex);
            ESP_LOGW(tag, "Sensor timeout %d @ %d", 1, k);
            return DHT_TIMEOUT_ERROR;
        }
        // high after 50us
        uSec = waitForLevel(75, 1);
        if (uSec < 0) {
            portEXIT_CRITICAL(&mutex);
            ESP_LOGW(tag, "Sensor timeout %d @ %d", 2, k);
            return DHT_TIMEOUT_ERROR;
        }
        // data bit after 26..28 us
        esp_rom_delay_us(40);

        if (gpio_get_level(dhtGpio))
            dhtData[byteInx] |= (1 << bitInx);

        // index to next byte
        if (bitInx == 0) {
            bitInx = 7;
            ++byteInx;
        } else {
            --bitInx;
        }
    }
    portEXIT_CRITICAL(&mutex);

    // == get humidity from Data[0] and Data[1] ==========================
    humidity = (((unsigned)dhtData[0] << 8) | dhtData[1]);

    // == get temp from Data[2] and Data[3]
    temperature = ((((unsigned)dhtData[2] & 0x7F) << 8) | dhtData[3]);

    if (dhtData[2] & 0x80) // negative temp
        temperature = -temperature;

    ESP_LOGD(tag, "DHT Response = %d, %d, %02x %02x %02x %02x %02x", uSec1, uSec2, dhtData[0], dhtData[1], dhtData[2], dhtData[3], dhtData[4]);

    // == verify if checksum is ok ===========================================
    // Checksum is the sum of Data 8 bits masked out 0xFF

    if (dhtData[4] == ((dhtData[0] + dhtData[1] + dhtData[2] + dhtData[3]) & 0xFF))
        return DHT_OK;
    else
        return DHT_CHECKSUM_ERROR;
}

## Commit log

2021-05-07 add CVE-Silent (1B)
    [Itho Data Labels.xlsx]
2024-12-01 Update to ESP-IDF 5.3, add multiple sensors support
    This change is not backward-compatible; after flashing need to
    reconfigure and enter sensor GPIO values again.
    [hru-com-esp32.fzz]
